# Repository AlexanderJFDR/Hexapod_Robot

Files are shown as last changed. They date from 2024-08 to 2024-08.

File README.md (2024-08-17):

# 六足机器人

## 整体介绍

该项目利用了暑假期间的时间，主要包括六足机器人的机械设计、硬件选择以及软件控制。
由于经费有限，项目未能制造出完整的六足机器人。但我们通过3D打印定制了一组支撑腿，
以验证逆运动学控制和上位机系统的正确性。

## 机械结构

六足机器人由六个支撑腿及身体组件构成，支撑腿提供行走、转动等动作，身体组件则用来
放置一些硬件设施。

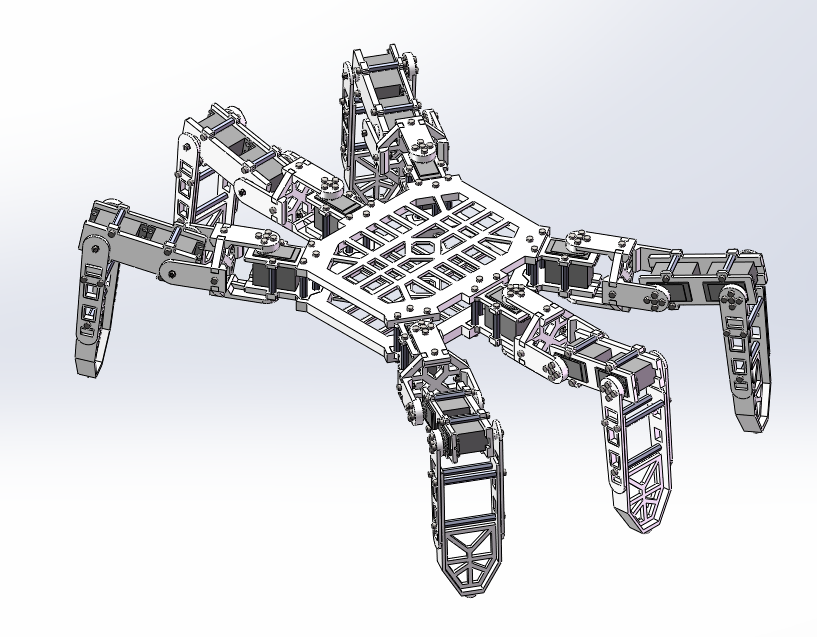
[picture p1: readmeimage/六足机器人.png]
六足机器人


每个支撑腿由3个**mg996r舵机**提供动力，并且被固定在身体组件上

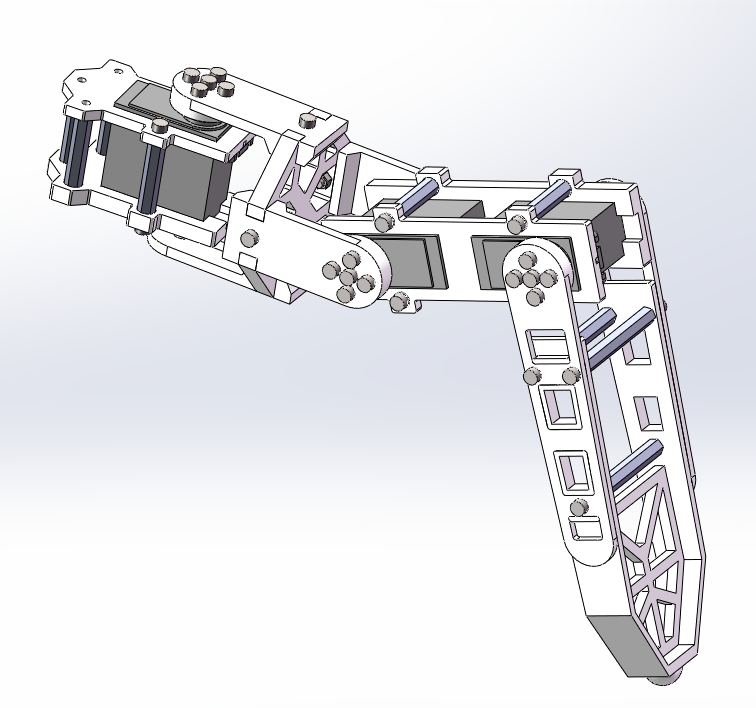
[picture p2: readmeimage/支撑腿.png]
支撑腿


六足机器人的大部分结构件采用3D打印制造，清单如下：
* 舵机上安装件×1×6
* 舵机下安装件×1×6
* 舵机上固定件×1×6
* 舵机下固定件×1×6
* 环形连接件×1×6
* 身体固定板_上板×1
* 身体固定板_下板×1
* 下肢驱动板×1×6
* 下肢被动板×1×6
* 下肢固定板×1×6
* 中段驱动板×1×6
* 中段被动板×1×6
* 中段驱动板_加强×1×6
* 中段被动板_加强×1×6

部分结构件及连接件采用标准件，具体见[标准件统计](机械结构/标准件统计.xlsx)

## 硬件系统

由于时间和实验条件的原因，本项目均采用成品开发板。电源采用**18650 12V 5600
mA锂电池组**，使用**LM2596S DC-DC直流可调降压稳压模块**为开发板提供5V电压
舵机控制板采用**Yeahbot 24路舵机控制板**,使用**DX-BT04-E02模块**提供蓝牙
通信支持，使用**ATK-USB-URAT-V1.2模块**提供USB转串口通讯支持。

## 软件控制

控制程序由python编写，主要分为[模型控制](软件控制/源代码/hexapod/models.py)、
[通讯控制](软件控制/源代码/hexapod/communication.py)和
[操作界面](软件控制/源代码/hexapod/interface.py)，控制软件已经被打包为
[.exe可执行文件](软件控制/打包程序/dist/run.exe)。

操作界面由工具栏和主界面构成。用户可以选择通信方式，并且发送数据到舵机控制板，舵机控制指令
参考[使用手册](硬件系统/YH-24路舵机控制板学习资料/01.使用手册/Yeahbot-24路舵机控制板使用手册.pdf)。

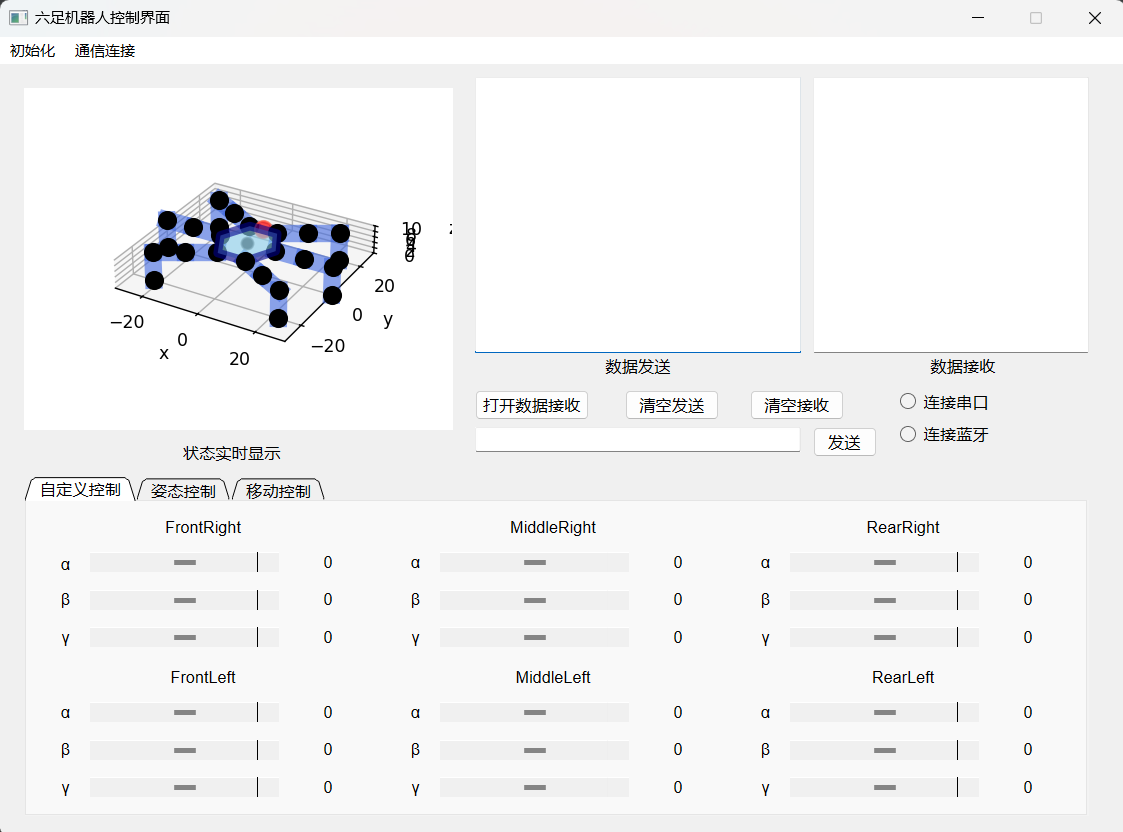
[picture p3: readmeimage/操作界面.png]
操作界面


初始化包括对body和leg的参数进行修改的子页面，可以对body的尺寸、初始位置做修改，还可以对
leg的尺寸、角度初始值、角度补偿、允许角度范围、基准坐标等修改。

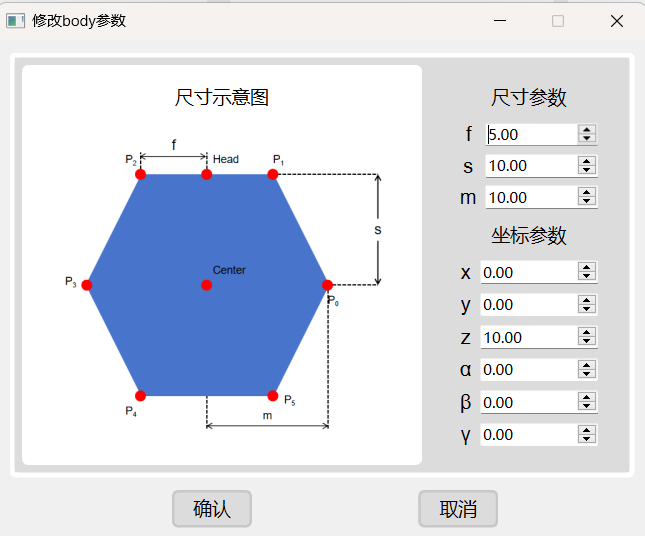
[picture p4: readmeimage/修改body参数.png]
修改body参数

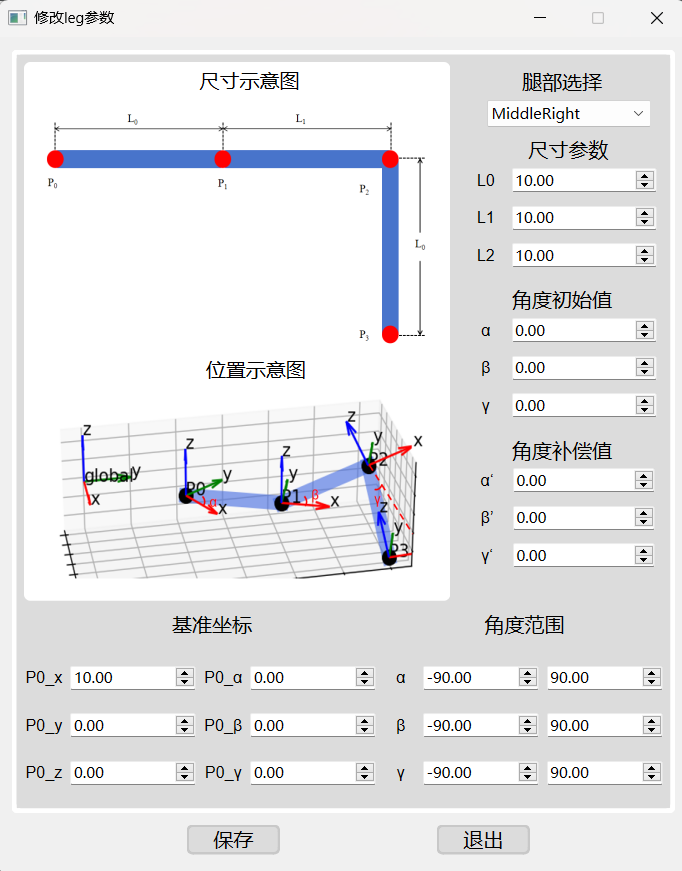
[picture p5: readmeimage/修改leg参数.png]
修改leg参数


通信连接包括串口通信和蓝牙通信的子页面，包括设置连接串口及蓝牙所需要的信息。

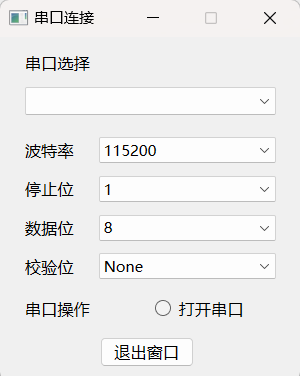
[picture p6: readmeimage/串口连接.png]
串口通信


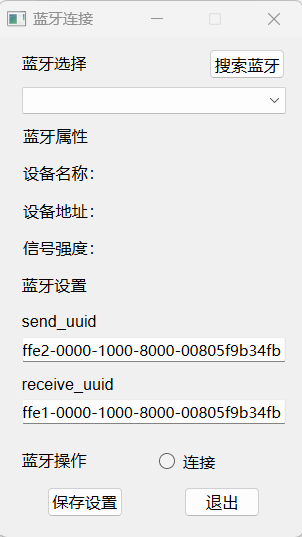
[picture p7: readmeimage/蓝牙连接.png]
蓝牙通信


下方分页面处包括自定义控制、姿态控制和移动控制。

自定义控制允许用户单独控制每个舵机角度，并且每个角度值是实时更新的。

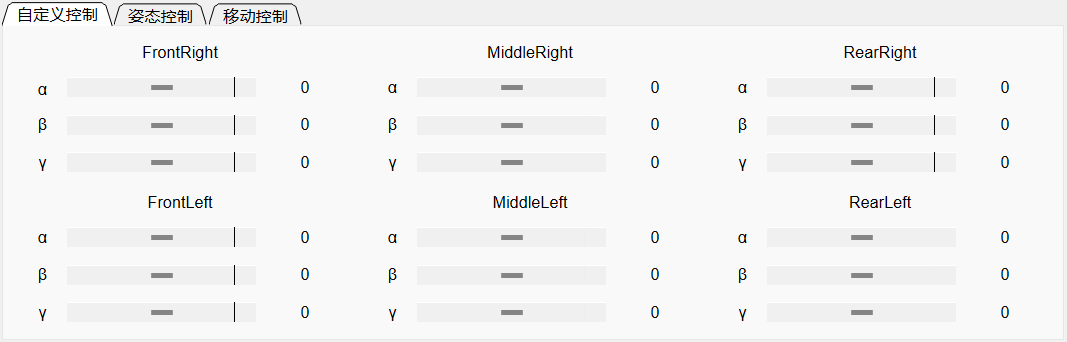
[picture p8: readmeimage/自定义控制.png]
自定义控制


姿态控制用于改变非移动状态下六足机器人的姿态，可以通过按键对姿态进行控制，
也可以通过右侧输入框来对姿态进行设置。

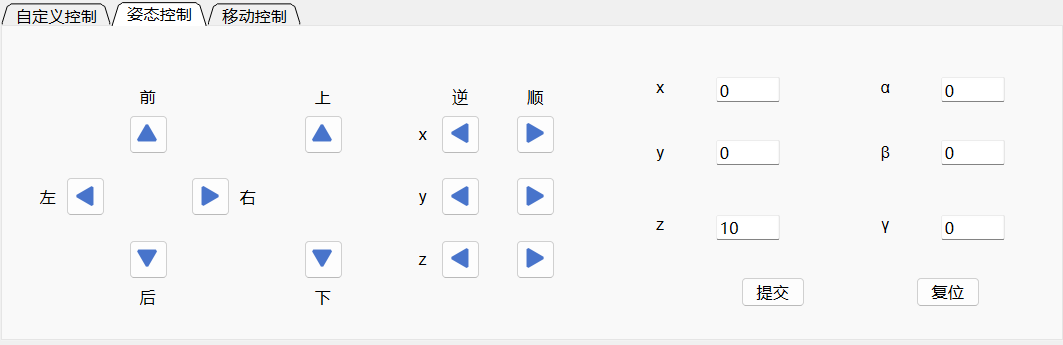
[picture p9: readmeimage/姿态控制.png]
姿态控制


移动控制用于控制六足机器人的前进、后退、转向等，可以选择三角步态或波动步态，
右侧自定义循环动作可以规定动作组，实现连续控制。

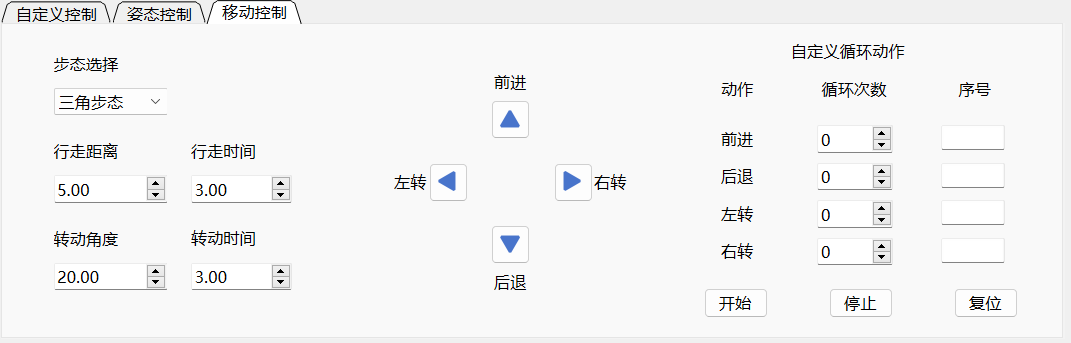
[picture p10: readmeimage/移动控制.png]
移动控制


## 机器人运动展示

移动姿态

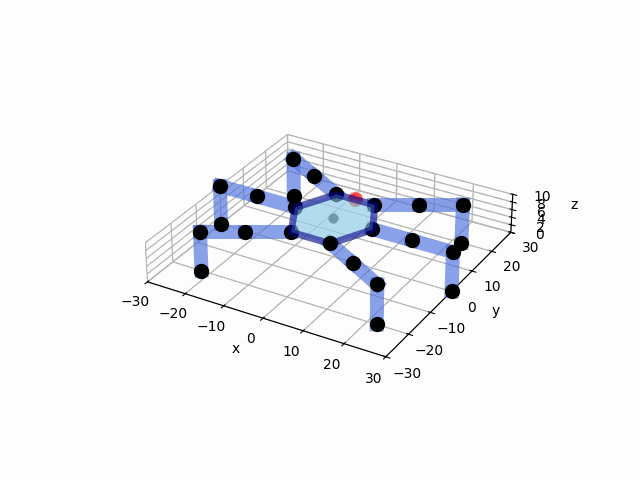
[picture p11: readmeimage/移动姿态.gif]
移动姿态


三角步态

三角步态

波动步态

波动步态

转向

转向

## LICENSE

本项目采用MIT许可证，更多详情请参见[LICENSE 文件](LICENSE.txt)。

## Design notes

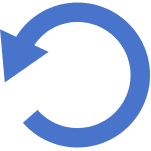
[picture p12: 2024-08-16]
软件控制/源代码/hexapod/image/rotate_arrow.png

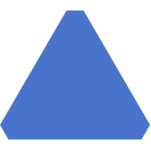
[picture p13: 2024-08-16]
软件控制/打包程序/dist/image/arrowhead_up.png

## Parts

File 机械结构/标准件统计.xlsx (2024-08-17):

类别 | 规格 | 数量
螺钉 | m3*10 | 54
 | m3*8 | 180
 | m3*14 | 78
螺柱 | m3*50 | 18
 | m3*30 | 54
轴承 | m3 | 18
螺母 | m3 | 42
舵盘 | m3 | 18

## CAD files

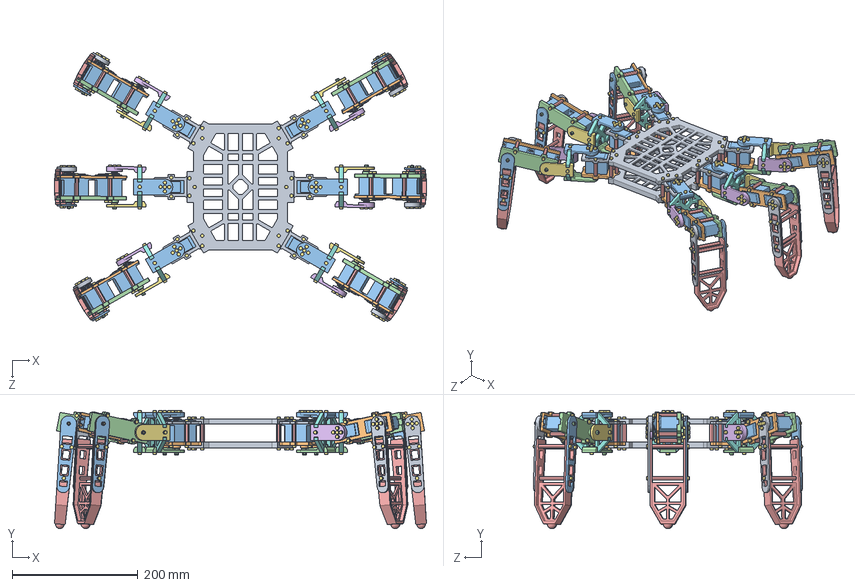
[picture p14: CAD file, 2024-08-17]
机械结构/六足机器人.SLDASM
590.6 x 187.6 x 428.1 mm
身体固定板 x 2
舵机上固定件 x 6
MG996r x 18
舵机下固定件 x 6
m3尼龙螺柱 x 72
m3_6垫片 x 48
m3螺钉 x 276
舵盘 x 18
下肢驱动板 x 6
m3_6止推轴承 x 18
下肢被动板 x 6
m3螺母 x 42
下肢固定板 x 6
中段驱动板 x 6
中段被动板 x 6
环形连接件 x 6
舵机上安装件 x 6
舵机下安装件 x 6
中段驱动板_加强 x 6
中段被动板_加强 x 6

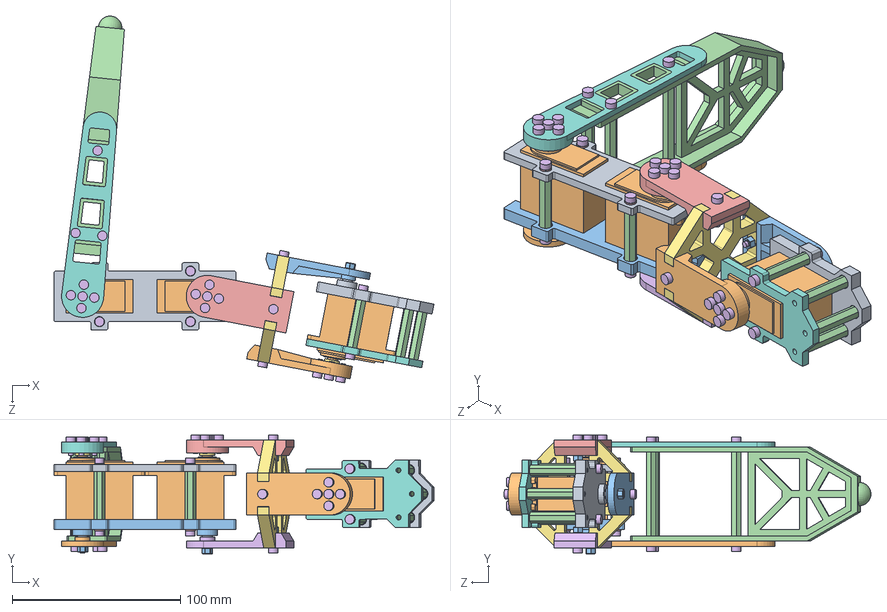
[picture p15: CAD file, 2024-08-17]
机械结构/支撑腿.SLDASM
225.6 x 70.5 x 217.8 mm
舵机上固定件
MG996r x 3
舵机下固定件
m3尼龙螺柱 x 12
m3_6垫片 x 8
m3螺钉 x 40
舵盘 x 3
下肢驱动板
m3_6止推轴承 x 3
下肢被动板
m3螺母 x 7
下肢固定板
中段驱动板
中段被动板
环形连接件
舵机上安装件
舵机下安装件
中段驱动板_加强
中段被动板_加强

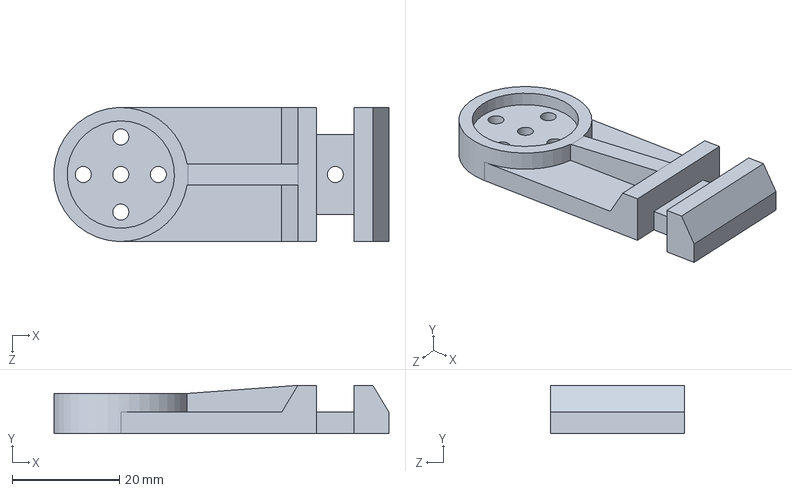
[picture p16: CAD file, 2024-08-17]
机械结构/中段驱动板_加强.SLDPRT
62.5 x 9.00 x 25.0 mm

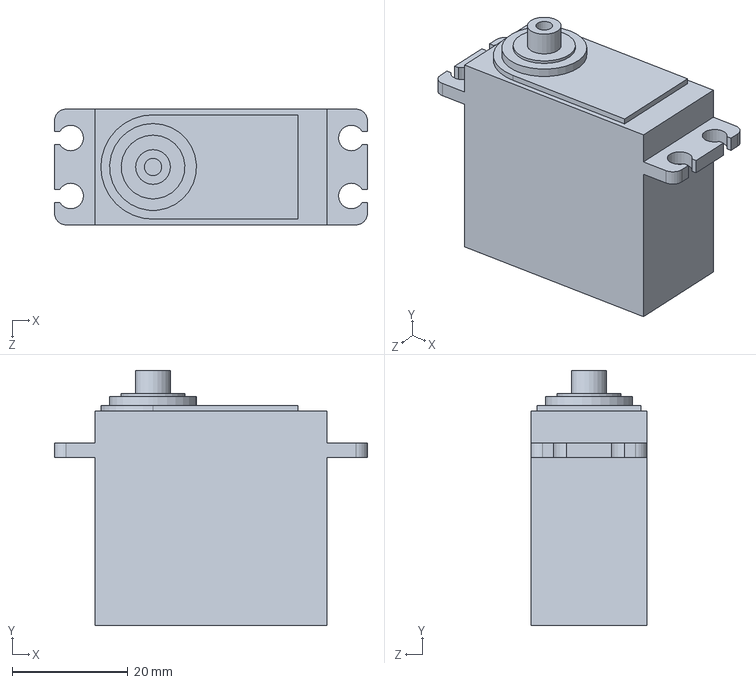
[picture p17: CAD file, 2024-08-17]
机械结构/MG996r.SLDPRT
54.0 x 44.0 x 20.0 mm

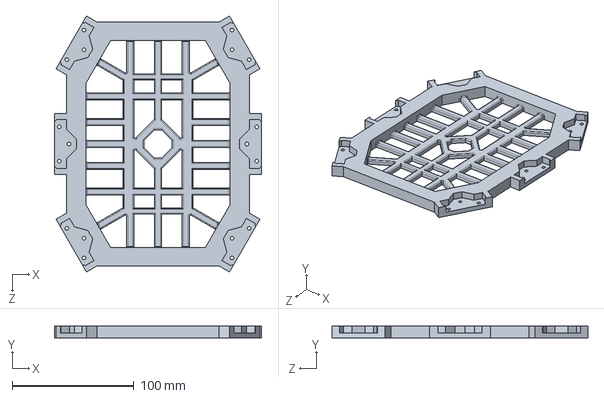
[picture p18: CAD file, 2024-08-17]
机械结构/身体固定板.SLDPRT
170.0 x 10.0 x 210.0 mm

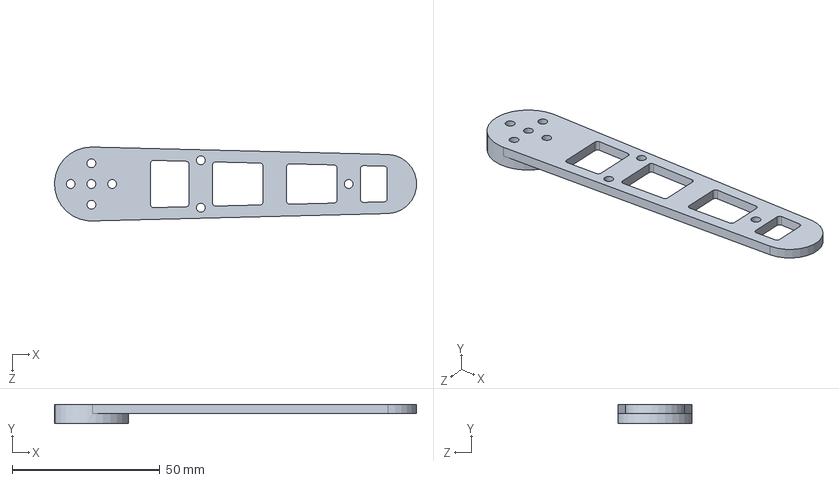
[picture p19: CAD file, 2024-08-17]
机械结构/下肢驱动板.SLDPRT
122.4 x 6.50 x 25.0 mm

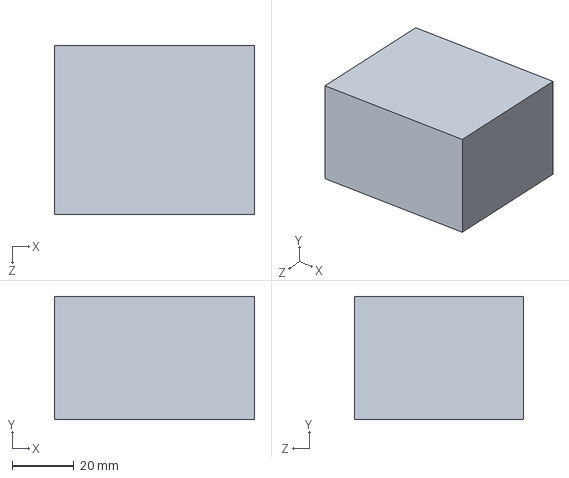
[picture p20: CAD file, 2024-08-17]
机械结构/电池.SLDPRT
65.0 x 40.0 x 55.0 mm

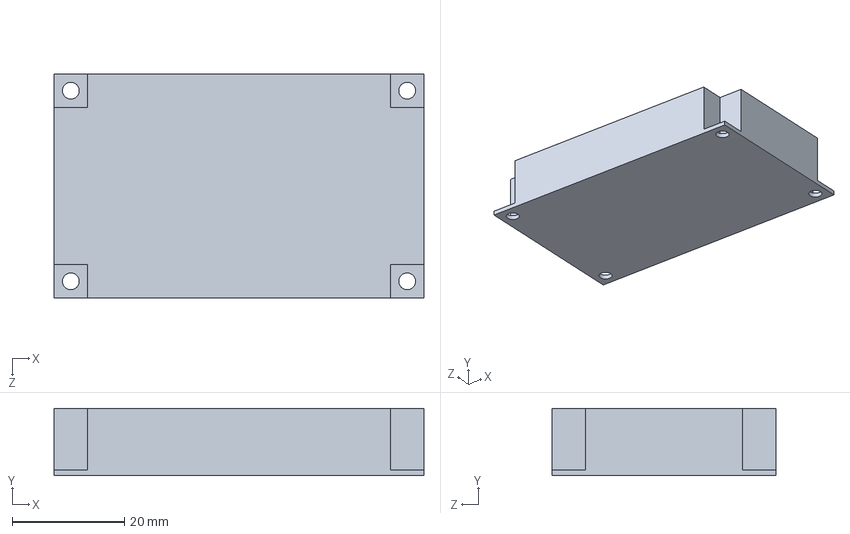
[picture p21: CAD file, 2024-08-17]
机械结构/降压模块.SLDPRT
66.0 x 12.0 x 40.0 mm

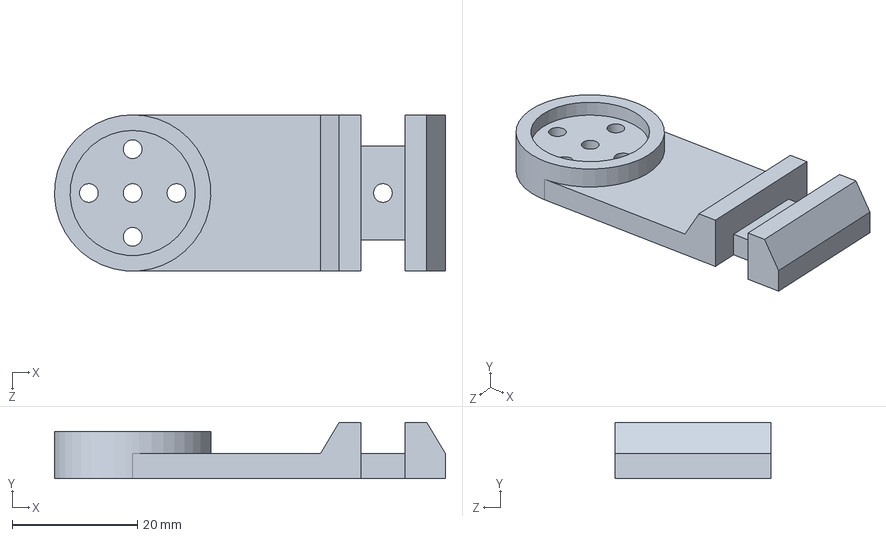
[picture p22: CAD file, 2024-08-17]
机械结构/中段驱动板.SLDPRT
62.5 x 9.00 x 25.0 mm

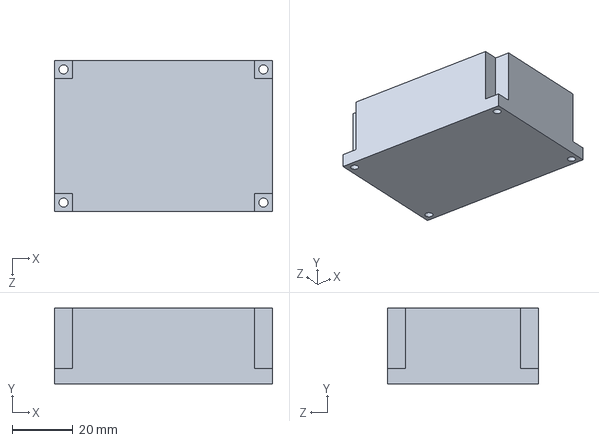
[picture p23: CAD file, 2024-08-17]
机械结构/舵机驱动板.SLDPRT
72.0 x 25.0 x 50.0 mm

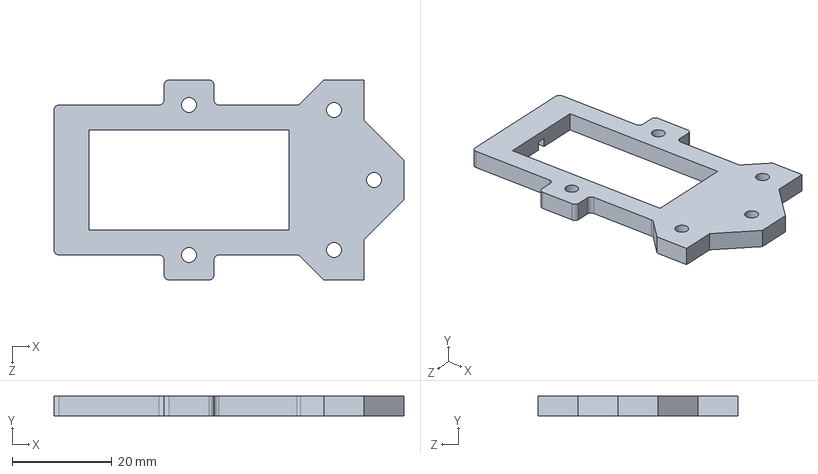
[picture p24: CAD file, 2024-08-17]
机械结构/舵机上安装件.SLDPRT
70.0 x 4.00 x 40.0 mm

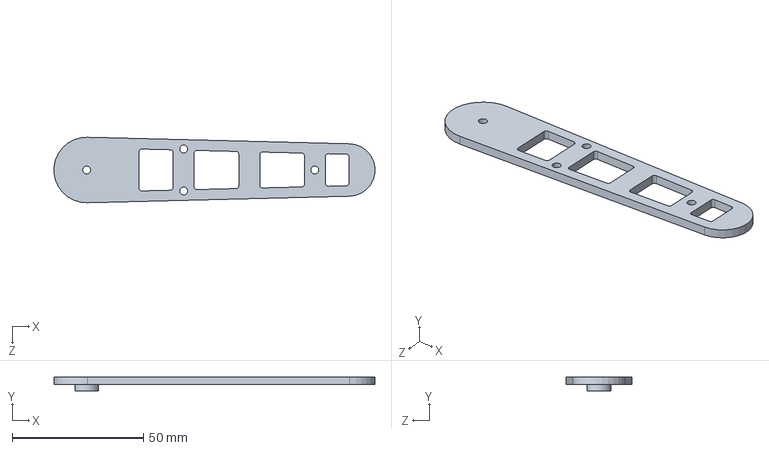
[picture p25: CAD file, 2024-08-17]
机械结构/下肢被动板.SLDPRT
122.4 x 5.50 x 25.0 mm

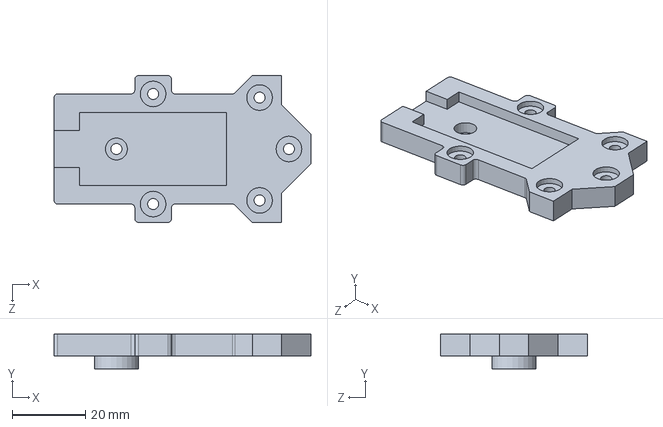
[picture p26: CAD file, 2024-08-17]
机械结构/舵机下安装件.SLDPRT
70.0 x 9.50 x 40.0 mm

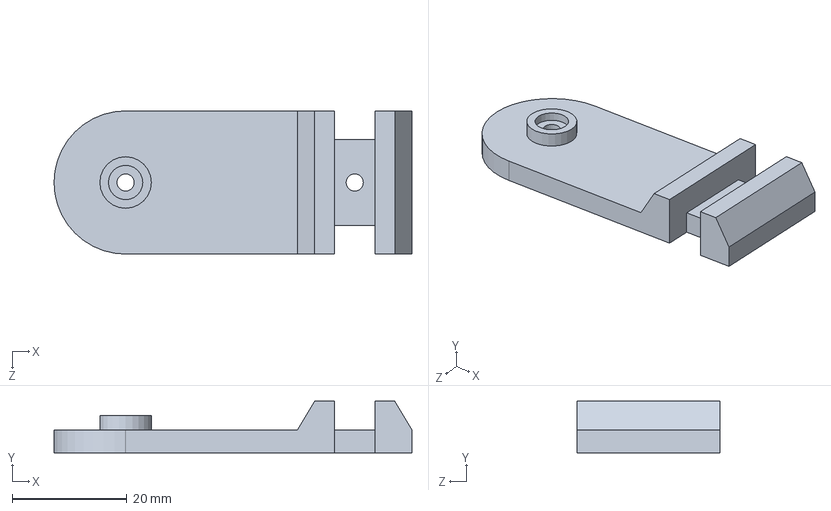
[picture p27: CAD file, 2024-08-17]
机械结构/中段被动板.SLDPRT
62.5 x 9.00 x 25.0 mm

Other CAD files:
软件控制/打包程序/dist/_internal/sphinx/templates/htmlhelp/project.stp
机械结构/舵盘.SLDPRT
机械结构/中段被动板_加强.SLDPRT
机械结构/摇臂.SLDPRT
机械结构/m2内十字螺钉.SLDPRT
机械结构/m2螺母.SLDPRT
机械结构/m3_6垫片.SLDPRT
机械结构/m3_6止推轴承.SLDPRT
机械结构/m3尼龙螺柱.SLDPRT
机械结构/m3螺母.SLDPRT
机械结构/m3螺钉.SLDPRT
机械结构/下肢固定板.SLDPRT
机械结构/环形连接件.SLDPRT
机械结构/舵机上固定件.SLDPRT
机械结构/舵机下固定件.SLDPRT

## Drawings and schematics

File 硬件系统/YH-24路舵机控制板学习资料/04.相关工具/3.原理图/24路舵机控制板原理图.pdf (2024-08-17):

# 电源输入

# 电源稳压

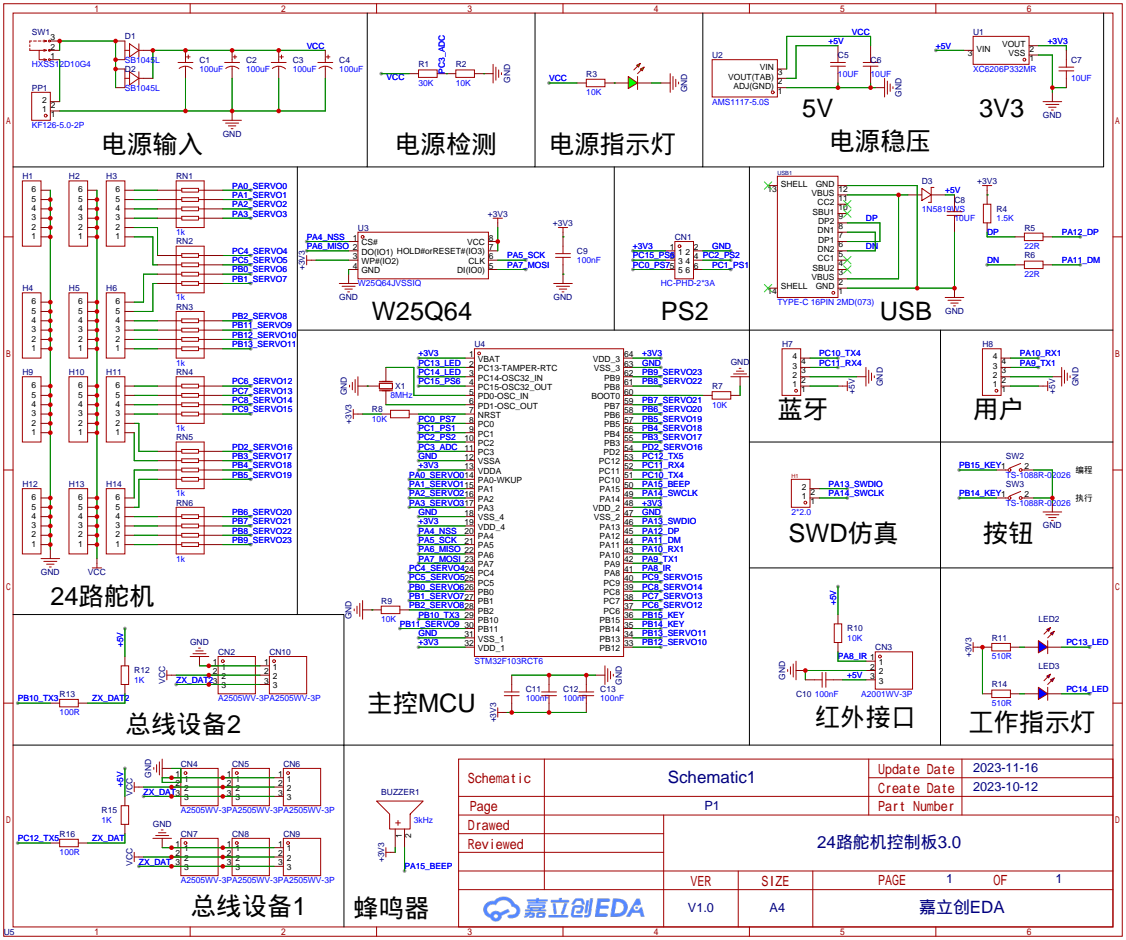
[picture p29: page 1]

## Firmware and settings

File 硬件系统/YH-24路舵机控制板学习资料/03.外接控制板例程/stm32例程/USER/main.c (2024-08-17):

/*
	单片机：STM32F103RCT6/STM32F103C8T6  倍频 72M 
	
	逻辑：
	初始化：串口1 2 3初始化，1 2为全双工串口，3为总线串口，即单线通信 
	主循环：隔10秒调用一次动作组
*/
#include "stm32f10x_conf.h"
#define tb_interrupt_open() {__enable_irq();}	//总中断打开
#define TB_USART1_COM 1
#define TB_USART2_COM 2
#define TB_USART3_COM 3

#define TB_USART_FLAG_ERR  0X0F
#define TB_USART_FLAG_RXNE 0X20
#define TB_USART_FLAG_TXE  0X80

#define tb_interrupt_open() {__enable_irq();}

#define uart1_open() 	{USART_ITConfig(USART1, USART_IT_RXNE, ENABLE);}
#define uart1_close() 	{USART_ITConfig(USART1, USART_IT_RXNE, DISABLE);}

#define uart2_open() 	{USART_ITConfig(USART2, USART_IT_RXNE, ENABLE);}		
#define uart2_close() 	{USART_ITConfig(USART2, USART_IT_RXNE, DISABLE);}		

#define uart3_open() 	{USART_ITConfig(USART3, USART_IT_RXNE, ENABLE);}		
#define uart3_close() 	{USART_ITConfig(USART3, USART_IT_RXNE, DISABLE);}		

void tb_usart_init(void);
void tb_usart1_init(u32 rate);
void tb_usart2_init(u32 rate);
void tb_usart3_init(u32 rate);

void tb_usart1_send_byte(u8 Data);
void tb_usart1_send_nbyte(u8 *Data, u16 size);
void tb_usart1_send_str(u8 *Data);

void tb_usart2_send_byte(u8 Data);
void tb_usart2_send_nbyte(u8 *Data, u16 size);
void tb_usart2_send_str(u8 *Data);

void tb_usart3_send_byte(u8 Data);
void tb_usart3_send_nbyte(u8 *Data, u16 size);
void tb_usart3_send_str(u8 *Data);

int tb_usart1_interrupt(void);
int tb_usart2_interrupt(void);
int tb_usart3_interrupt(void);

void uart1_send_str(u8 *str);
void uart1_send_nbyte(u8 *Data, u16 size);
void uart1_send_byte(u8 data);

void uart2_send_str(u8 *str);
void uart2_send_nbyte(u8 *Data, u16 size);
void uart2_send_byte(u8 data);

void zx_uart_send_str(u8 *str);
void uart3_send_str(u8 *str);
void uart3_send_nbyte(u8 *Data, u16 size);
void uart3_send_byte(u8 data);


void rcc_init(void);							//主频设置
void delay_ms(unsigned int t);		//毫秒级别延时


int main(void) {	
	rcc_init();				//主频设置72M
	tb_usart_init();		//初始化串口
	tb_interrupt_open();	//总中断打开
	while(1) {	
		uart1_send_str((u8 *)"$DGT:0-4,1!");	//串口1 调用 0到4 动作，执行1次 其他命令参照控制器指令
		zx_uart_send_str((u8 *)"$DGT:0-4,1!");	//总线口 调用 0到4 动作，执行1次 其他命令参照控制器指令
		delay_ms(10000);						//延时10秒	
	}
}

void rcc_init(void) {
	ErrorStatus HSEStartUpStatus;
	RCC_DeInit();
	RCC_HSEConfig(RCC_HSE_ON); 
	HSEStartUpStatus = RCC_WaitForHSEStartUp();
	while(HSEStartUpStatus == ERROR);
	RCC_HCLKConfig(RCC_SYSCLK_Div1);//SYSCLK
	RCC_PCLK1Config(RCC_HCLK_Div2);//APB1  MAX = 36M
	RCC_PCLK2Config(RCC_HCLK_Div1);//APB2  MAX = 72M
	RCC_PLLConfig(RCC_PLLSource_HSE_Div1, RCC_PLLMul_9);
	RCC_PLLCmd(ENABLE); 
	while(RCC_GetFlagStatus(RCC_FLAG_PLLRDY) == RESET);
	RCC_SYSCLKConfig(RCC_SYSCLKSource_PLLCLK);
	while(RCC_GetSYSCLKSource() != 0x08);
}


void delay_ms(unsigned int t) {
	int t1;
	while(t--) {
		t1 = 7200;
		while(t1--);
	}
}

void tb_usart_init(void) {
	tb_usart1_init(115200);
	uart1_open();
	
	tb_usart2_init(115200);
	uart2_open();
	
	tb_usart3_init(115200);
	uart3_open();
	
	tb_interrupt_open();
	return;
}


void tb_usart1_init(u32 rate) {  
    GPIO_InitTypeDef GPIO_InitStructure;  
    USART_InitTypeDef USART_InitStructure; 
	USART_ClockInitTypeDef USART_ClockInitStructure; 	
    NVIC_InitTypeDef NVIC_InitStructure;  
  
	
    RCC_APB2PeriphClockCmd(RCC_APB2Periph_GPIOA | RCC_APB2Periph_USART1, ENABLE);  
    USART_DeInit(USART1);  
    /* Configure USART Tx as alternate function push-pull */  
    GPIO_InitStructure.GPIO_Pin = GPIO_Pin_9;  
    GPIO_InitStructure.GPIO_Speed = GPIO_Speed_50MHz;  
	GPIO_InitStructure.GPIO_Mode = GPIO_Mode_AF_PP;  
    GPIO_Init(GPIOA, &GPIO_InitStructure);  
      
    /* Configure USART Rx as input floating */  
    GPIO_InitStructure.GPIO_Pin = GPIO_Pin_10;  
	GPIO_InitStructure.GPIO_Mode = GPIO_Mode_IN_FLOATING;  
    GPIO_Init(GPIOA, &GPIO_InitStructure);  
  
    USART_InitStructure.USART_BaudRate = rate;  
    USART_InitStructure.USART_WordLength = USART_WordLength_8b;  
    USART_InitStructure.USART_StopBits = USART_StopBits_1;  
    USART_InitStructure.USART_Parity = USART_Parity_No;  
    USART_InitStructure.USART_HardwareFlowControl = USART_HardwareFlowControl_None;  
    USART_InitStructure.USART_Mode = USART_Mode_Rx | USART_Mode_Tx;  
    
	USART_ClockInitStructure.USART_Clock = USART_Clock_Disable;  
    USART_ClockInitStructure.USART_CPOL = USART_CPOL_Low;  
    USART_ClockInitStructure.USART_CPHA = USART_CPHA_2Edge;  
    USART_ClockInitStructure.USART_LastBit = USART_LastBit_Disable;  
    USART_ClockInit(USART1, &USART_ClockInitStructure);  
	USART_Init(USART1, &USART_InitStructure );   
  
	NVIC_PriorityGroupConfig(NVIC_PriorityGroup_0);
    NVIC_InitStructure.NVIC_IRQChannel = USART1_IRQn;  
    NVIC_InitStructure.NVIC_IRQChannelPreemptionPriority = 1;  
    NVIC_InitStructure.NVIC_IRQChannelSubPriority = 1;  
    NVIC_InitStructure.NVIC_IRQChannelCmd = ENABLE;  
    NVIC_Init(&NVIC_InitStructure); 
	
	USART_ITConfig(USART1, USART_IT_RXNE, ENABLE);
    //USART_ITConfig(USART1, USART_IT_TXE, ENABLE);
	
//	USART_ITConfig(USART1, USART_IT_PE, ENABLE);
//	USART_ITConfig(USART1, USART_IT_ERR, ENABLE);

	USART_Cmd(USART1, ENABLE);  
}  
  
void tb_usart2_init(u32 rate) {  
	GPIO_InitTypeDef GPIO_InitStructure;  
    USART_InitTypeDef USART_InitStructure;   
	NVIC_InitTypeDef NVIC_InitStructure; 
	
	RCC_APB2PeriphClockCmd(RCC_APB2Periph_GPIOA, ENABLE);  
    RCC_APB1PeriphClockCmd(RCC_APB1Periph_USART2, ENABLE);  
    USART_DeInit(USART2);  
    /* Configure USART Tx as alternate function push-pull */  
    GPIO_InitStructure.GPIO_Pin = GPIO_Pin_2;  
    GPIO_InitStructure.GPIO_Speed = GPIO_Speed_50MHz;  
	GPIO_InitStructure.GPIO_Mode = GPIO_Mode_AF_PP;  
    GPIO_Init(GPIOA, &GPIO_InitStructure);  
      
    /* Configure USART Rx as input floating */  
    GPIO_InitStructure.GPIO_Pin = GPIO_Pin_3;  
	GPIO_InitStructure.GPIO_Mode = GPIO_Mode_IN_FLOATING;  
    GPIO_Init(GPIOA, &GPIO_InitStructure);  
	
    USART_InitStructure.USART_BaudRate = rate;  
    USART_InitStructure.USART_WordLength = USART_WordLength_8b;  
    USART_InitStructure.USART_StopBits = USART_StopBits_1;  
    USART_InitStructure.USART_Parity = USART_Parity_No;  
    USART_InitStructure.USART_HardwareFlowControl = USART_HardwareFlowControl_None;  
    USART_InitStructure.USART_Mode = USART_Mode_Rx | USART_Mode_Tx;  
	USART_Init(USART2, &USART_InitStructure );   
	
	NVIC_InitStructure.NVIC_IRQChannel = USART2_IRQn;
    NVIC_InitStructure.NVIC_IRQChannelPreemptionPriority = 1;
    NVIC_InitStructure.NVIC_IRQChannelSubPriority = 2;
    NVIC_InitStructure.NVIC_IRQChannelCmd = ENABLE;
    NVIC_Init(&NVIC_InitStructure);   
	
	USART_ITConfig(USART2, USART_IT_RXNE, ENABLE);
    //USART_ITConfig(USART2, USART_IT_TXE, ENABLE);
	
//	USART_ITConfig(USART2, USART_IT_PE, ENABLE);
//	USART_ITConfig(USART2, USART_IT_ERR, ENABLE);
	
	USART_Cmd(USART2, ENABLE); 
} 

void tb_usart3_init(u32 rate) {  
	GPIO_InitTypeDef GPIO_InitStructure;  
    USART_InitTypeDef USART_InitStructure;   
	NVIC_InitTypeDef NVIC_InitStructure; 
	
	
	/* config USART3 clock */
	RCC_APB2PeriphClockCmd(RCC_APB2Periph_GPIOB, ENABLE);
	RCC_APB1PeriphClockCmd(RCC_APB1Periph_USART3, ENABLE);
	
	/* USART3 GPIO config */
	/* Configure USART3 Tx (PB.10) as alternate function push-pull */
	GPIO_InitStructure.GPIO_Pin = GPIO_Pin_10;
	GPIO_InitStructure.GPIO_Mode = GPIO_Mode_AF_PP;
	GPIO_InitStructure.GPIO_Speed = GPIO_Speed_50MHz;
	GPIO_Init(GPIOB, &GPIO_InitStructure);    
	
	/* Configure USART3 Rx (PB.11) as input floating */
	GPIO_InitStructure.GPIO_Pin = GPIO_Pin_11;
	GPIO_InitStructure.GPIO_Mode = GPIO_Mode_IN_FLOATING;
	GPIO_Init(GPIOB, &GPIO_InitStructure);
	
	/* USART3 mode config */
	USART_InitStructure.USART_BaudRate = rate;
	USART_InitStructure.USART_WordLength = USART_WordLength_8b;
	USART_InitStructure.USART_StopBits = USART_StopBits_1;
	USART_InitStructure.USART_Parity = USART_Parity_No ;
	USART_InitStructure.USART_HardwareFlowControl = USART_HardwareFlowControl_None;
	USART_InitStructure.USART_Mode = USART_Mode_Rx | USART_Mode_Tx;
	USART_Init(USART3, &USART_InitStructure);
		
	NVIC_InitStructure.NVIC_IRQChannel = USART3_IRQn;
    NVIC_InitStructure.NVIC_IRQChannelPreemptionPriority = 1;
    NVIC_InitStructure.NVIC_IRQChannelSubPriority = 3;
    NVIC_InitStructure.NVIC_IRQChannelCmd = ENABLE;
    NVIC_Init(&NVIC_InitStructure);   
	
	USART_ITConfig(USART3, USART_IT_RXNE, ENABLE);
    //USART_ITConfig(USART3, USART_IT_TXE, ENABLE);
	
	USART_HalfDuplexCmd(USART3,ENABLE);
		
	USART_Cmd(USART3, ENABLE); 
} 

void tb_usart1_send_byte(u8 Data) {
	USART_SendData(USART1, Data);
	return;
}

void tb_usart1_send_nbyte(u8 *Data, u16 size) {
	u16 i = 0;
	for(i=0; i<size; i++) {
		USART_SendData(USART1, Data[i]);
		while(USART_GetFlagStatus(USART1, USART_FLAG_TXE) == RESET); 
	}
	return;
}
void tb_usart1_send_str(u8 *Data) {
	while(*Data) {
		USART_SendData(USART1, *Data++);
		while(USART_GetFlagStatus(USART1, USART_FLAG_TXE) == RESET); 
	}
	return;
}

void tb_usart2_send_byte(u8 Data) {
	USART_SendData(USART2, Data);
	return;
}

void tb_usart2_send_nbyte(u8 *Data, u16 size) {
	u16 i = 0;
	for(i=0; i<size; i++) {
		USART_SendData(USART2, Data[i]);
		while(USART_GetFlagStatus(USART2, USART_FLAG_TXE) == RESET); 
	}
	return;
}
void tb_usart2_send_str(u8 *Data) {
	while(*Data) {
		USART_SendData(USART2, *Data++);
		while(USART_GetFlagStatus(USART2, USART_FLAG_TXE) == RESET); 
	}
	return;
}

void tb_usart3_send_byte(u8 Data) {
	USART_SendData(USART3, Data);
	return;
}

void tb_usart3_send_nbyte(u8 *Data, u16 size) {
	u16 i = 0;
	for(i=0; i<size; i++) {
		USART_SendData(USART3, Data[i]);
		while(USART_GetFlagStatus(USART3, USART_FLAG_TXE) == RESET); 
	}
	return;
}
void tb_usart3_send_str(u8 *Data) {
	while(*Data) {
		USART_SendData(USART3, *Data++);
		while(USART_GetFlagStatus(USART3, USART_FLAG_TXE) == RESET); 
	}
	return;
}


/**========================串口中断=============================**/
int USART1_IRQHandler(void) {
	u8 sbuf_bak;
	static u16 buf_index = 0;

	if(USART_GetFlagStatus(USART1,USART_IT_RXNE)==SET) {
		USART_ClearITPendingBit(USART1, USART_IT_RXNE);		
		sbuf_bak = USART_ReceiveData(USART1); 

	}
	
	//if(USART_GetITStatus(USART1, USART_IT_TXE) != RESET) {   
		//USART_SendData(USARTy, TxBuffer1[TxCounter1++]);
	//}   
	return 0;
}

int USART2_IRQHandler(void) { 
	if(USART_GetFlagStatus(USART2,USART_IT_RXNE)==SET) {
		USART_ClearITPendingBit(USART2, USART_IT_RXNE);		
	
			
	}
	
	//if(USART_GetITStatus(USART2, USART_IT_TXE) != RESET) {   
	//	USART_SendData(USARTy, TxBuffer1[TxCounter1++]);
	//}  
	return 0;
}

int USART3_IRQHandler(void) { 
	u8 sbuf_bak;
	static u16 buf_index = 0;
	if(USART_GetFlagStatus(USART3,USART_IT_RXNE)==SET) {
		USART_ClearITPendingBit(USART3, USART_IT_RXNE);	
		sbuf_bak = USART_ReceiveData(USART3);			
	}
	
	//if(USART_GetITStatus(USART3, USART_IT_TXE) != RESET) {   
	//	USART_SendData(USARTy, TxBuffer1[TxCounter1++]);
	//}  
	return 0;
}



void uart1_send_str(u8 *str) {
	tb_usart1_send_str(str);
}

void uart1_send_nbyte(u8 *Data, u16 size) {
	tb_usart1_send_nbyte(Data, size);
}

void uart1_send_byte(u8 data) {
	tb_usart1_send_byte(data);
}



void uart2_send_str(u8 *str) {
	tb_usart2_send_str(str);	
}


void uart2_send_nbyte(u8 *Data, u16 size) {
	tb_usart2_send_nbyte(Data, size);
}

void uart2_send_byte(u8 data) {
	tb_usart2_send_byte(data);
}


void zx_uart_send_str(u8 *str) {
	tb_usart3_send_str(str);	
}


void uart3_send_str(u8 *str) {
	tb_usart3_send_str(str);	
}


void uart3_send_nbyte(u8 *Data, u16 size) {
	tb_usart3_send_nbyte(Data, size);
}

void uart3_send_byte(u8 data) {
	tb_usart3_send_byte(data);
}

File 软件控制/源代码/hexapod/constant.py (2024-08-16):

import math
#Body参数
BODY_SIZE=(5,10,10)
BODY_ATTITUDE=(0,0,10,0,0,0)
#Leg参数
LEG_LENGTH=[10,10,10]
LEG_ANGLE=[0,0,0]
ANGLE_BIAS=[0,0,0]
ANGLE_LIMITS=[(-math.pi/2, math.pi/2), (-math.pi/2, math.pi/2), (-math.pi/2, math.pi/2)]
#Hexapod参数
HEXAPOD_LEG_LENGTH=[[10,10,10],[10,10,10],[10,10,10],[10,10,10],[10,10,10],[10,10,10]]
HEXAPOD_LEG_ANGLE=[[0,0,0],[0,0,0],[0,0,0],[0,0,0],[0,0,0],[0,0,0]]
HEXAPOD_LEG_ANGLE1=[[0,0,0],[0,0,0],[0,0,0],[0,0,0],[0,0,0],[0,0,0]]
HEXAPOD_ANGLE_BIAS=[[0,0,0],[0,0,0],[0,0,0],[0,0,0],[0,0,0],[0,0,0]]
HEXAPOD_ANGLE_LIMITS=[[(-math.pi/2,math.pi/2),(-math.pi/2, math.pi/2),(-math.pi/2, math.pi/2)],
                      [(-math.pi/2, math.pi/2), (-math.pi/2, math.pi/2), (-math.pi/2, math.pi/2)],
                      [(-math.pi/2, math.pi/2), (-math.pi/2, math.pi/2), (-math.pi/2, math.pi/2)],
                      [(-math.pi/2, math.pi/2), (-math.pi/2, math.pi/2), (-math.pi/2, math.pi/2)],
                      [(-math.pi/2, math.pi/2), (-math.pi/2, math.pi/2), (-math.pi/2, math.pi/2)],
                      [(-math.pi/2, math.pi/2), (-math.pi/2, math.pi/2), (-math.pi/2, math.pi/2)]]
HEXAPOD_LEG_ROT=((0,0,0),(0,0,math.pi/6),(0,0,5*math.pi/6),(0,0,math.pi),(0,0,-5*math.pi/6),(0,0,-math.pi/6))
LEG_ID_NAMES = {0: "MiddleRight", 1:"FrontRight", 2:"FrontLeft",
                3: "MiddleLeft", 4:"RearLeft", 5:"RearRight"}
STATE_NAMES = {0: ""}
#串口参数
PORT = 'COM3'
BAUDRATE = 115200
BYTESIZE = 8
STOPBITES = 1
#蓝牙参数
TARGETADDRESS = '98:DA:F0:00:77:FD'
TARGETNAME = 'BT18-T'
BLUETOOTHPORT = 1
SENDUUID = '0000ffe2-0000-1000-8000-00805f9b34fb'
RECEIVEUUID = '0000ffe1-0000-1000-8000-00805f9b34fb'

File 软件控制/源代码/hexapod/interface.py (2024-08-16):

from PyQt6.QtCore import pyqtSignal, Qt, QThread, QTimer
from PyQt6.QtGui import QImage, QPixmap
from PyQt6.QtWidgets import QApplication, QMainWindow, QWidget, QDialog, QComboBox, QMessageBox, QRadioButton, \
    QVBoxLayout
from PyQt6 import QtCore, QtGui, QtWidgets
import sys
import threading

from matplotlib.backends.backend_qt5agg import FigureCanvasQTAgg as FigureCanvas

from models import *
from communication import *

#定义主窗口
class mainWindow(QMainWindow):
    #初始化
    def __init__(self,hexapod:Hexapod,ser:Serial,blt:Bluetooth):
        super().__init__()
        #串口线程
        self.SERthread = SERIALThread(ser)
        self.SERthread.start()
        #蓝牙线程
        self.BLTthread = BLTThread(blt)
        self.BLTthread.start()

        #初始化主窗口页面
        self.init_UI(hexapod)
        #菜单信号
        self.actionbody.triggered.connect(lambda: self.myWidget1.show_widget(hexapod))
        self.actionleg.triggered.connect(lambda: self.myWidget2.show_widget(hexapod))
        self.actionserial.triggered.connect(lambda: self.myWidget3.show_widget())
        self.actionbluetooth.triggered.connect(lambda: self.myWidget4.show_widget())
        #界面同步信号
        self.myWidget1.update_body_aignal.connect(lambda: self.mainWidget.init_control(hexapod))
        self.myWidget2.update_leg_aignal.connect(lambda: self.mainWidget.init_control(hexapod))
        #加载qss
        # with open("style/Aqua.qss", "r") as file:
        #     self.setStyleSheet(file.read())
        #显示窗口
        self.show()
    #初始化界面
    def init_UI(self, hexapod:Hexapod):
        self.setObjectName("mainWindow")
        self.setFixedSize(900, 640)
        #子窗口创建
        self.myWidget1 = myWidget1(hexapod)
        self.myWidget2 = myWidget2(hexapod)
        self.myWidget3 = myWidget3(self.SERthread)
        self.myWidget4 = myWidget4(self.BLTthread)
        #菜单棒设置
        self.menubar = QtWidgets.QMenuBar()
        self.menubar.setGeometry(QtCore.QRect(0, 0, 747, 22))
        self.menubar.setObjectName("menubar")
        #菜单选项1设置
        self.menu = QtWidgets.QMenu(parent=self)
        self.menu.setObjectName("menu")
        self.actionbody = QtGui.QAction(parent=self)
        self.actionbody.setObjectName("actionbody")
        self.actionleg = QtGui.QAction(parent=self)
        self.actionleg.setObjectName("actionleg")
        self.menu.addAction(self.actionbody)
        self.menu.addAction(self.actionleg)
        self.menubar.addAction(self.menu.menuAction())
        # 菜单选项2设置
        self.menu_2 = QtWidgets.QMenu(parent=self.menubar)
        self.menu_2.setObjectName("menu_2")
        self.actionserial = QtGui.QAction(parent=self)
        self.actionserial.setObjectName("actionserial")
        self.actionbluetooth = QtGui.QAction(parent=self)
        self.actionbluetooth.setObjectName("actionbluetooth")
        self.menu_2.addAction(self.actionserial)
        self.menu_2.addAction(self.actionbluetooth)
        self.menubar.addAction(self.menu_2.menuAction())
        #主窗口创建
        self.mainWidget = mainWidget(self.SERthread,self.BLTthread,hexapod)
        self.setCentralWidget(self.mainWidget)

        self.setMenuBar(self.menubar)
        self.retranslateUi()
        QtCore.QMetaObject.connectSlotsByName(self)
    #控件属性定义
    def retranslateUi(self):
        _translate = QtCore.QCoreApplication.translate
        self.setWindowTitle(_translate("MainWindow", "六足机器人控制界面"))
        self.menu.setTitle(_translate("MainWindow", "初始化"))
        self.menu_2.setTitle(_translate("MainWindow", "通信连接"))
        self.actionbody.setText(_translate("MainWindow", "body"))
        self.actionleg.setText(_translate("MainWindow", "leg"))
        self.actionserial.setText(_translate("MainWindow", "serial"))
        self.actionbluetooth.setText(_translate("MainWindow", "bluetooth"))

#子类化QComboBox
class myComboBox(QComboBox):
    clicked = pyqtSignal()  # 自定义信号
    def mousePressEvent(self, event):
        self.clicked.emit()  # 触发自定义信号
        super().mousePressEvent(event)  # 确保默认行为仍然发生

#定义串口子线程
class SERIALThread(QThread):
    #定义返回值
    devices_list = pyqtSignal(list)
    connect_res = pyqtSignal(bool)
    disconnect_res = pyqtSignal(bool)
    is_open_signal = pyqtSignal(bool)
    is_receive_signal = pyqtSignal(bool)
    paramters_list = pyqtSignal(tuple)
    send_message = pyqtSignal(str)
    receive_message = pyqtSignal(str)
    #自定义构造函数传参
    def __init__(self, ser:Serial):
        super().__init__()
        self.loop = asyncio.new_event_loop()
        self.serial = ser
        self.is_send = True
        self.is_receive = False
    def run(self):
        asyncio.set_event_loop(self.loop)
        self.loop.run_until_complete(self.main_loop())
    #监听循环
    async def main_loop(self):
        while True:
            if self.is_receive and self.serial.is_open:
                await self.receive_data()
            await asyncio.sleep(0.1)
    #扫描可用串口
    async def scan(self):
        devices = await asyncio.to_thread(self.serial.select_com)
        self.devices_list.emit(devices)
    #连接串口
    async def connect_ser(self):
        is_open = await asyncio.to_thread(self.serial.open_serial)
        self.connect_res.emit(is_open)
    #断开串口
    async def disconnect_ser(self):
        await asyncio.to_thread(self.serial.close_serial)
        self.disconnect_res.emit(self.serial.is_open)
    #读取连接状态
    async def read_is_open(self):
        self.is_open_signal.emit(self.serial.is_open)
    #读取是否接收信息
    async def read_is_receive(self):
        self.is_receive_signal.emit(self.is_receive)
    # 停止发送
    async def stop_send(self):
        self.is_send = False
        await asyncio.sleep(1)
        self.is_send = True
    #修改接收状态
    async def update_is_receive(self,is_receive):
        self.is_receive = is_receive
    #修改参数
    async def update_paramters(self,paramters):
        await asyncio.to_thread(self.serial.update_paramters,paramters)
    #获取参数
    async def get_paramters(self):
        paramters = await asyncio.to_thread(self.serial.get_paramters)
        self.paramters_list.emit(paramters)
    #发送信息
    async def send_data(self,data):
        if self.is_send:
            await asyncio.to_thread(self.serial.send_info,data)
            data = self.serial.name + ':' + data
            self.send_message.emit(data)
    #接收信息
    async def receive_data(self):
        data = await asyncio.to_thread(self.serial.receive_data)
        if data != None:
            data = self.serial.name + ':' + data
            self.receive_message.emit(data)
    #发送coding
    async def send_coding(self,coding):
        for item in coding:
            if self.is_send:
                string, time = item
                await self.send_data(string)
                await asyncio.sleep(time)
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

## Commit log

2024-08-17 修改机械结构
    [MG996r.SLDPRT, 下肢被动板.SLDPRT, 下肢驱动板.SLDPRT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]
2024-08-17 机械结构修改
    [六足机器人.SLDASM, 标准件统计.xlsx]
2024-08-17 修改README
    [标准件统计.xlsx]
